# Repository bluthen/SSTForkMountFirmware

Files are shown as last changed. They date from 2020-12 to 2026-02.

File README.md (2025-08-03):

# SST Forkmount

This repo contains the electronic designs and software for [StarSync Trackers](https://starsynctrackers.com/)
computerized forkmount equatorial mounts. It was designed to work with SST hardware but should work with any fork mount
that uses steppers for motors.

## Component Structure

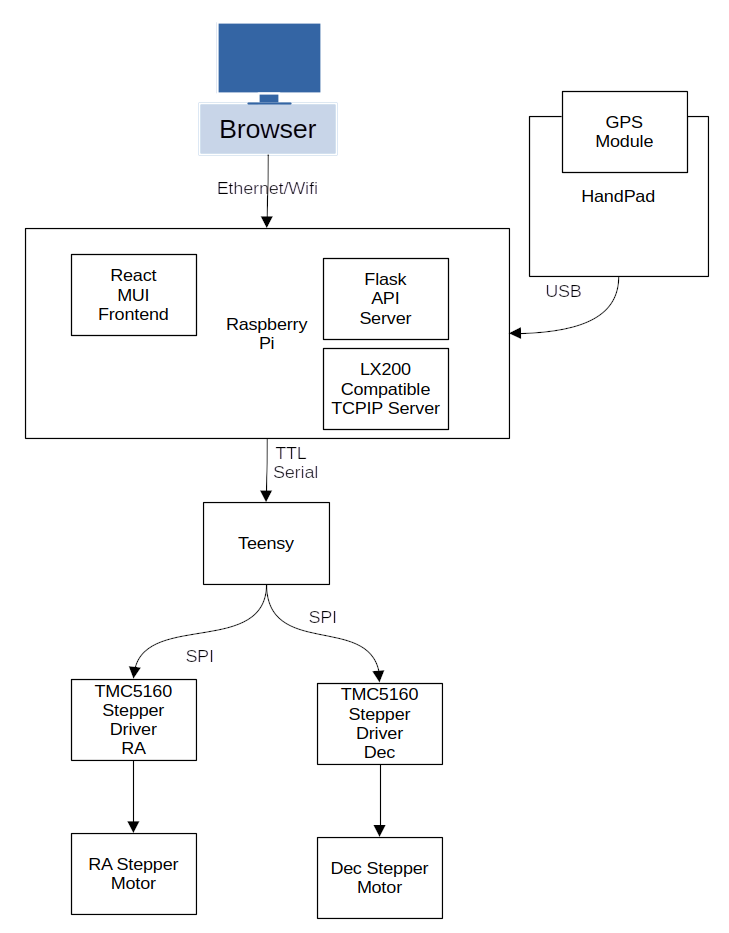
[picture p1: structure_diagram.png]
Diagram image on how the different components work together to make up the mount


Below it tries to describe

* Computer connects to the mount through Ethernet or Wifi and control the telescope in one of the following ways.
    * A web browser [SST Discovery Tool](https://github.com/bluthen/SSTForkMountDiscovery)
    * software capable of communicating through a LX200 protocol
* Handpad is a device attached through a USB cable
    * It has a GPS moduled embedded inside it that can give the telescope accurate time and location.
    * Has a interface to control the telescope without a computer attached, with goto and manual slew functions.
* Raspberry pi has a controller board (Pi Hat) attached to it and has three main components.
    * Flask API Server - Provides a REST like API to control the telescope
    * React MUI Frontend - web based user interface to communcate with the API Server
    * LX200 Compatible TCPIP Server - An alternative way to control the telescope through a dedicated TCP/IP Port.
* Motor Control Chain
    * Microcontroller (Teensy) - The Raspberry pi has a controller board attached and communicates with it through TTL
      Serial.
    * The Microcontroller (Teensy) - communicates with stepper drivers using SPI Protocol and step/direction protocol.
    * The stepper drivers (TMC5160) - controls the RA/Dec steppers to point the telescope

# Project directory structure

* [electronics](electronics) - Files related to the hardware of: Handpad, serial to ethernet, main controller
    * [enclosures](electronics/enclosures) - Enclosures to house electronics
    * [firmware](electronics/firmware) - Microcontroller firmware
    * [pcb](electronics/pcb) - Schematic and PCB files
* [piside](piside) - Software the run on the Pi.
    * [client_advanced_slew_limits](piside/client_advanced_slew_limits) - Slew limits UI component
    * [client_main](pisiude/client_main) - The Material UI web client
    * [server](piside/server) - Flask API Server

# TODOs

* Improve a test Error modeling
    * Add Star Alignment to handpad that uses the error modeling feature
    * Good prompts for error modeling/alignment to web ui
* Script and instructions to generate object and city elevation database `ssteq.sqlite`
* More python type-hinting
* Switch from Flask to [FastAPI](https://fastapi.tiangolo.com/)
* Cleanup files piside/server in director submodules
* Better testing of encoder usage
* Easier pi setup
* Instructions for settings.json for docker usage
* Alt/Az Mode

# Screenshots

Screen shots of the web client.

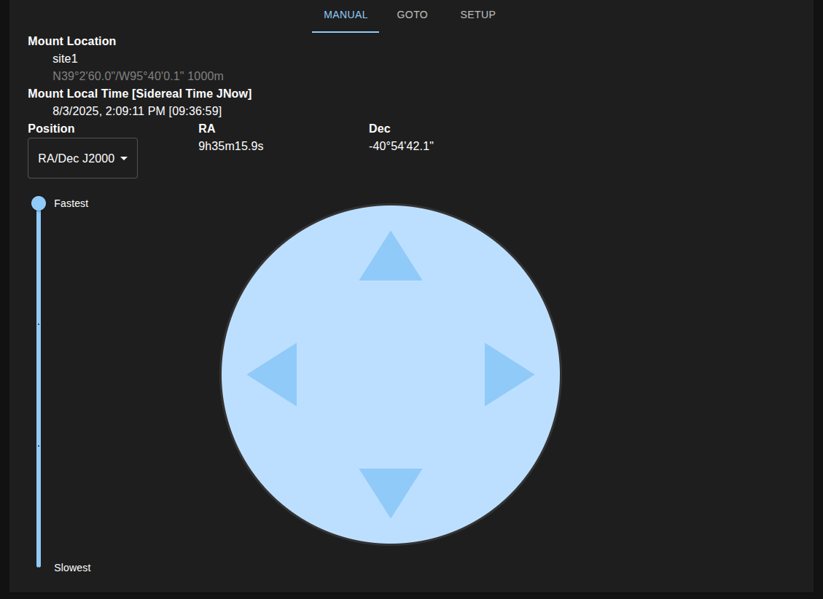
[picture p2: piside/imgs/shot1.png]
Screen shot of web client software running, circle in middle control directions, side vertical slider for speed.


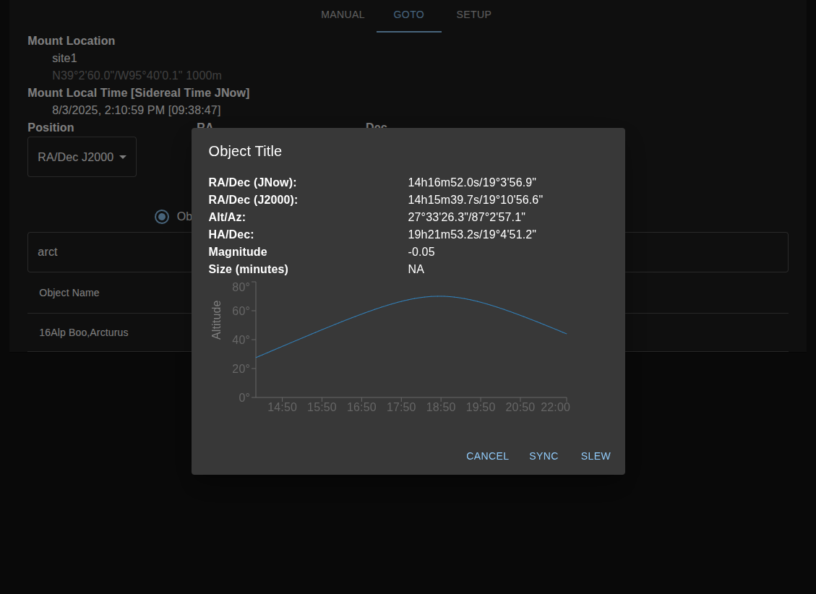
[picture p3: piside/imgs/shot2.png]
Screen shot of web client software running, a graph with time and altitude of Arcuturus with coordinates listed


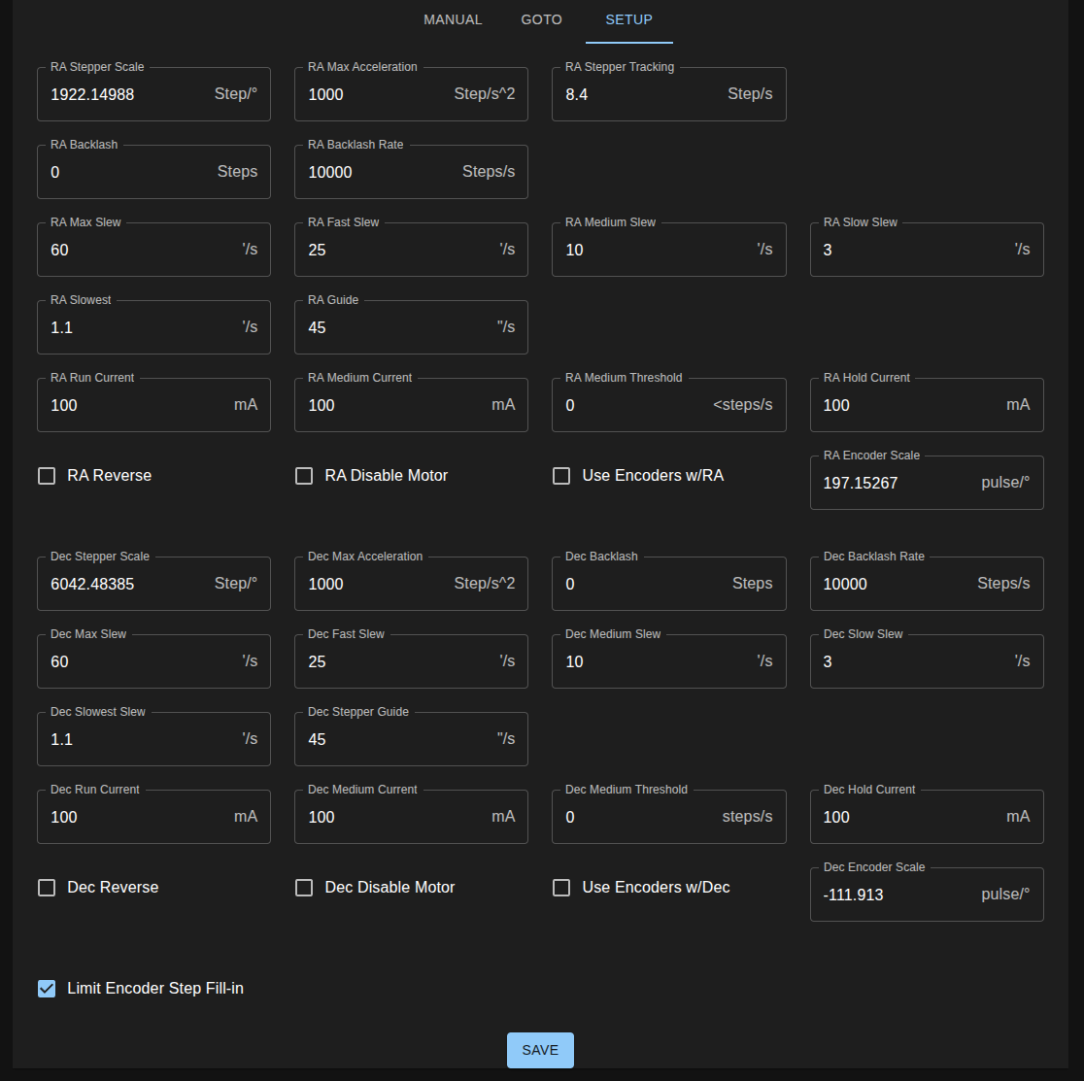
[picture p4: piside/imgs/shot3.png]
Screen shot of web client software running, advanced configuration window showing settings like steps per degrees, backlash, acceleration


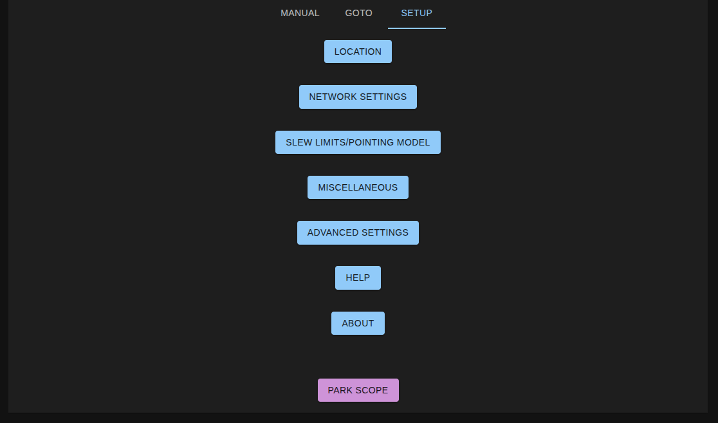
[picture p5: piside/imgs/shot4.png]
Screen shot of web client software running, setup menu with a set of buttons to different configuration screens


# Related projects

If you are interested in this project, some of these other open source projects might interest you.

* [OnStep](https://github.com/hjd1964/OnStep)
* [AstroEQ](https://www.astroeq.co.uk/)
* [TeenAstro](https://groups.io/g/TeenAstro)

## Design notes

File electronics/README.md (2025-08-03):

# SST Electronics Hardware

## PiHat/SSTFork Stepper Micro

This is the electronics that take communication from the Pi and control the stepper motors.

## Handpad

This is the electronics of the handpad. A handheld device, with a display, to control the telescope mount.

## Serial to Ethernet

This is a small device that creates a serial port on the host computer and sends back and forth all communication on the
serial port to a IP_ADDRESS:Port through Ethernet.

This could be handy for older software that can only communicate with LX200 Protocol through a serial port.

**Computer** <-USB Serial-> **serial_to_ethernet** <-Ethernet-> **Device/Fork Mount**

# Directroy Structure

See each section for more information.

* [enclosures](enclosures) - Enclosure to house electronics
* [firmware](firmware) - Microcontroller firmware files
* [pcb](pcb) - Schematic and PCB for electronics

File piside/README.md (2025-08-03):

# PiSide - Software that runs on the Pi

Screen shot of web client software running, circle in middle control directions, side vertical slider for speed.

Screen shot of web client software running, a graph with time and altitude of Arcuturus with coordinates listed

Screen shot of web client software running, advanced configuration window showing settings like steps per degrees, backlash, acceleration

Screen shot of web client software running, setup menu with a set of buttons to different configuration screens

# Docker compose

You can run the software in docker with a simulated microcontroller board.

* `settings.json` - needs to be set up correctly
* `ssteq.sqlite` - needs to be generated (gen script and documentation are on TODO list)
* `server/simulation_files` - may need to be set up

```bash
docker compose build
docker compose up
```

Open browser to: [http://localhost:5001](http://localhost:5001)

# Package Management: Local Development vs on Pi

Two package managers are used depending on if you are development on your desktop or development/running on the Pi.
Mainly so the package manager could be configured to utilize [Pi Wheels](https://www.piwheels.org/)

* [Pipenv](https://pipenv.pypa.io/en/latest/) was used for dependencies on the PI. Here we are able to
  utilize [Pi Wheels](https://www.piwheels.org/)
* [Poetry](https://python-poetry.org/) is used for desktop development

# Directory structure

* [server](server) - API Server
* [client_main](client_main) - Material UI based web client
* [client_advanced_slew_limits](client_advanced_slew_limits) - A web interface sub app to set slew limits written in
  jquery
* [setup](setup) - Setup documentation and files

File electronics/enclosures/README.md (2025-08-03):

# Enclosures

**NOTE: For handpad enclosures see [handpad](handpad)**

The enclosures are designed in [FreeCad](https://www.freecad.org/).

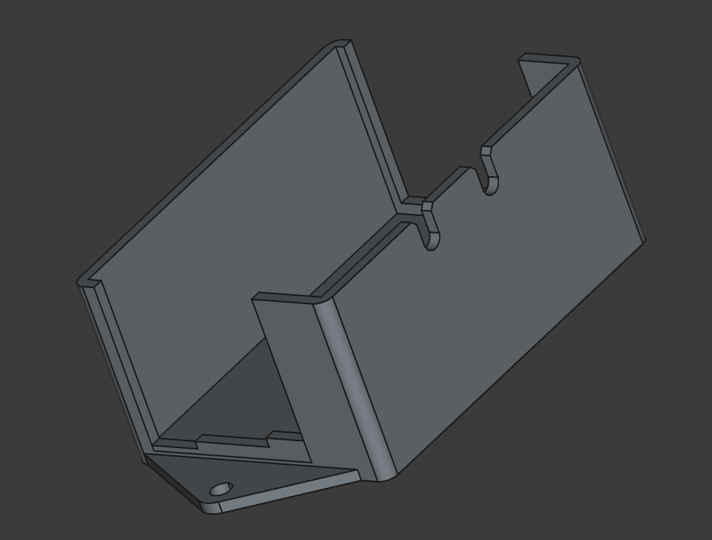
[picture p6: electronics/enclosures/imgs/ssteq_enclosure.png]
Render of main electronics enclosure model


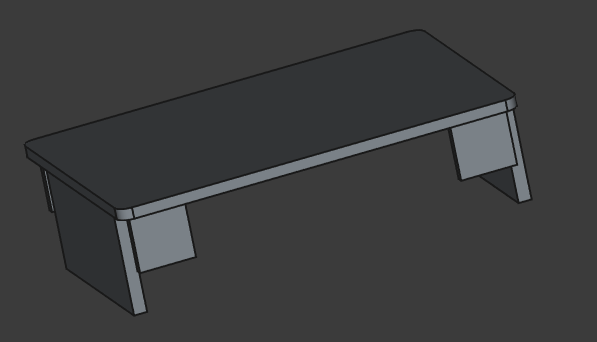
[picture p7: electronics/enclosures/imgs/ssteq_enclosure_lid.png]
Render of main electronics enclosure lid model


Render of a standoff model

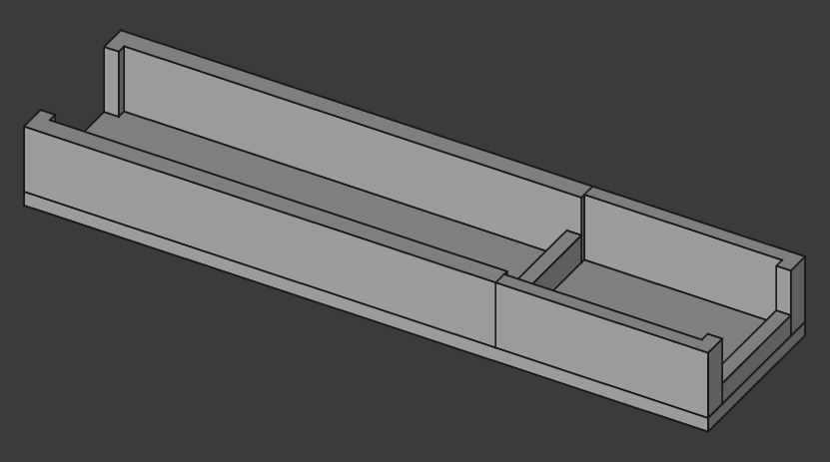
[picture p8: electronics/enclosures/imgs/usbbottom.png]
Render of Enclosure to hold Serial to Ethernet model bottom


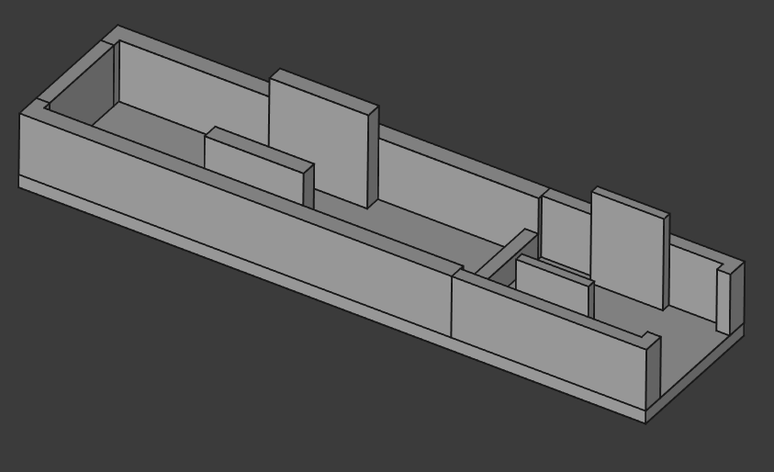
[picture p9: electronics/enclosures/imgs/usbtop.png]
Render of Enclosure to hold Serial to Ethernet model top


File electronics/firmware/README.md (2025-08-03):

# Electronics Firmware

This contains the firmware for microcontrollers.

* [sstfork_stepper_micro](sstfork_stepper_micro) - Firmware that controls the stepper drivers/steppers.
* [handpad](handpad) - Firmware for the microcontroller in the handpad.
* [serial_to_ethernet](serial_to_ethernet) - Firmware for the microcontroller the serial to ethernet bridge.

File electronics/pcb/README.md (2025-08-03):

# PCBs and Schematics

The PCBs are made in an Open Source Electronics Design Suite [KiCad](https://kicadstudio.com/).

## PiHat (Motor Controller)

The device that takes communication from the Pi that controls the stepper motors.

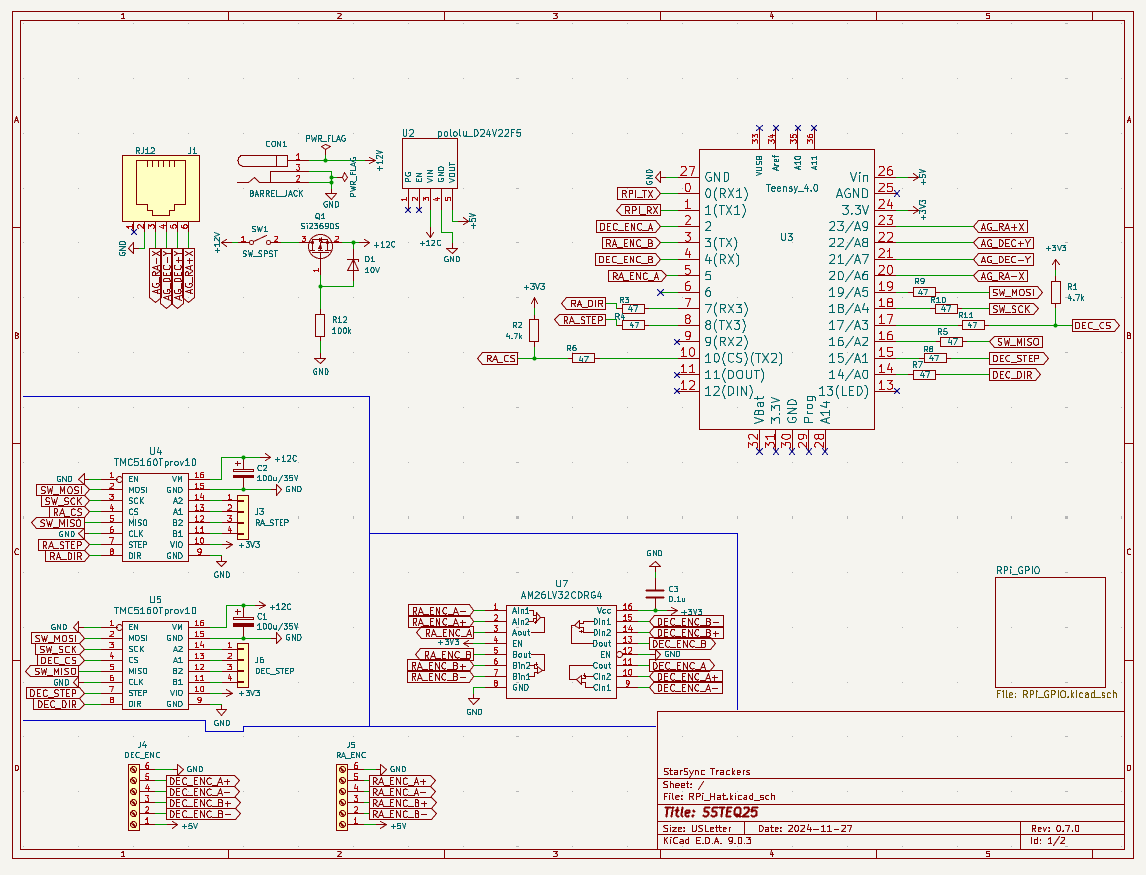
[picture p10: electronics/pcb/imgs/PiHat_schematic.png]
Screenshot from KiCad of PiHat schematic


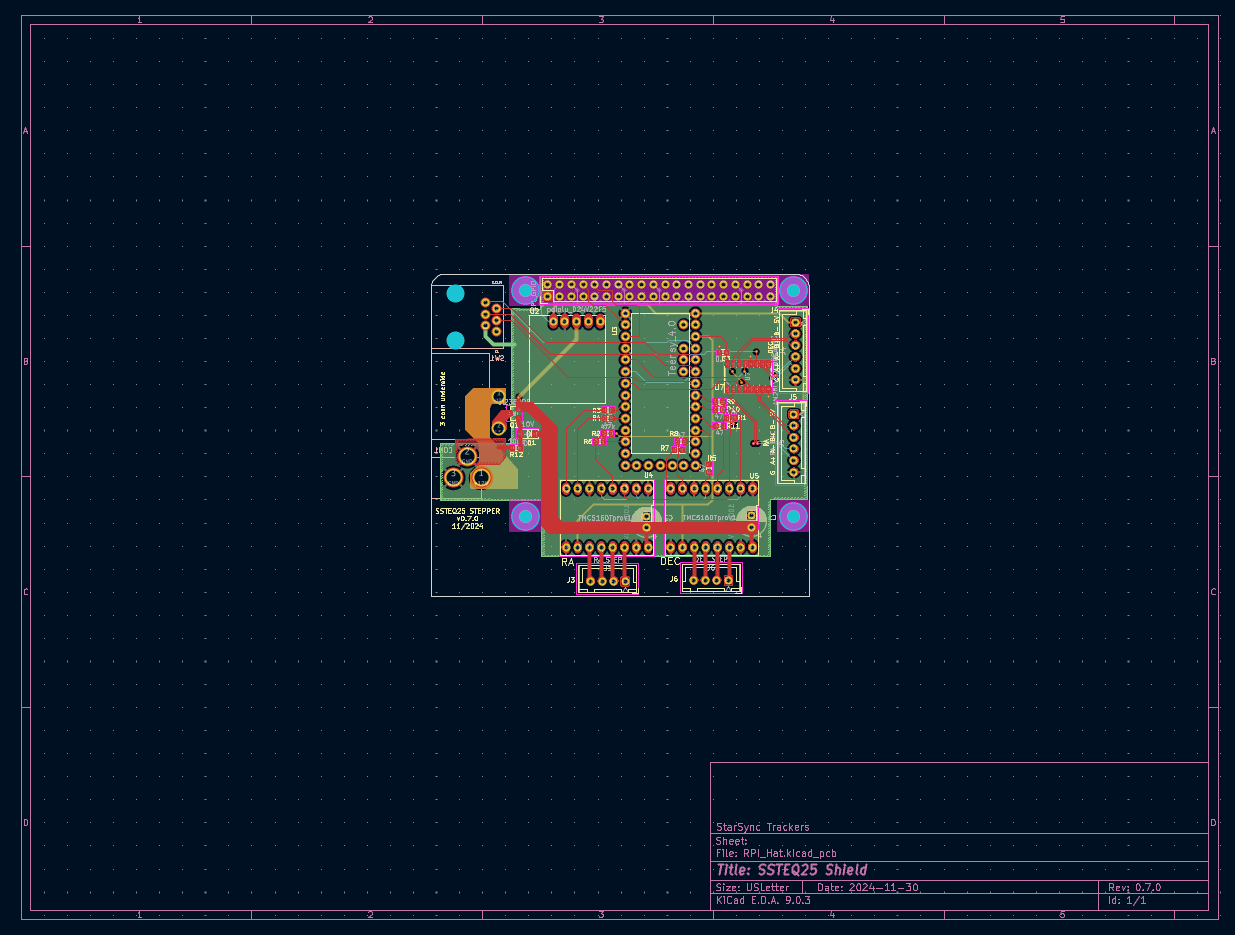
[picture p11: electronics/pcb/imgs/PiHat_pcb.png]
Screenshot from KiCad of PiHat PCB Layout


## Handpad

Handpad that lets you control the mount without a computer. Useful when next to the mount or using it for visual work.

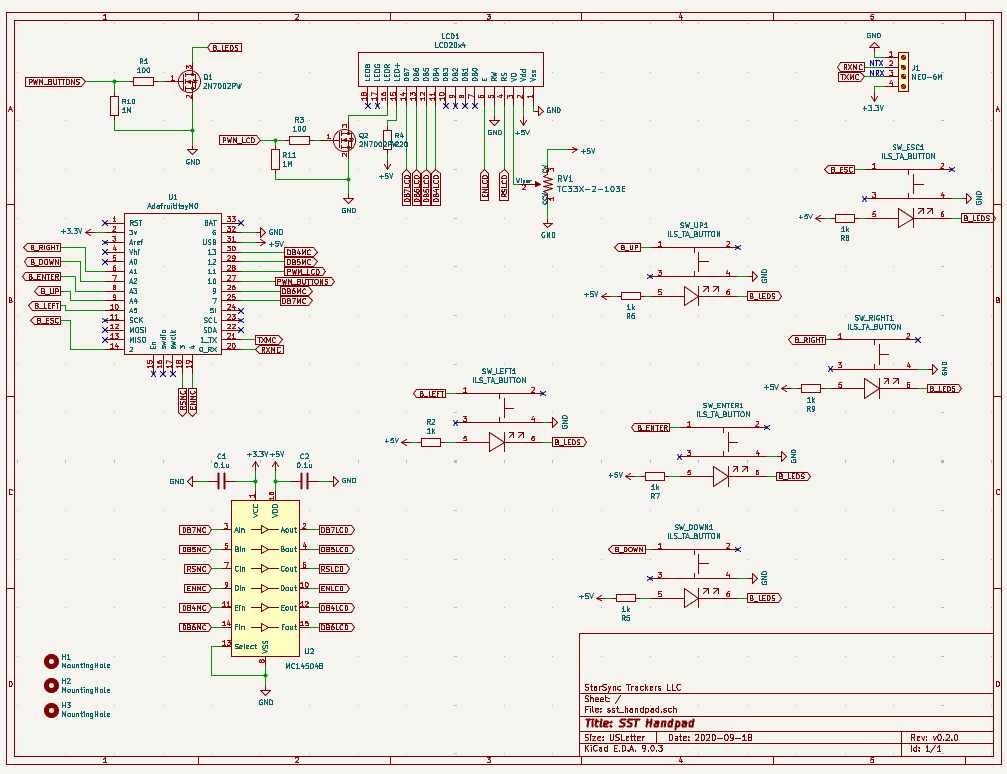
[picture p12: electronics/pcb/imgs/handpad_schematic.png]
Screenshot from KiCad of Handpad schematic


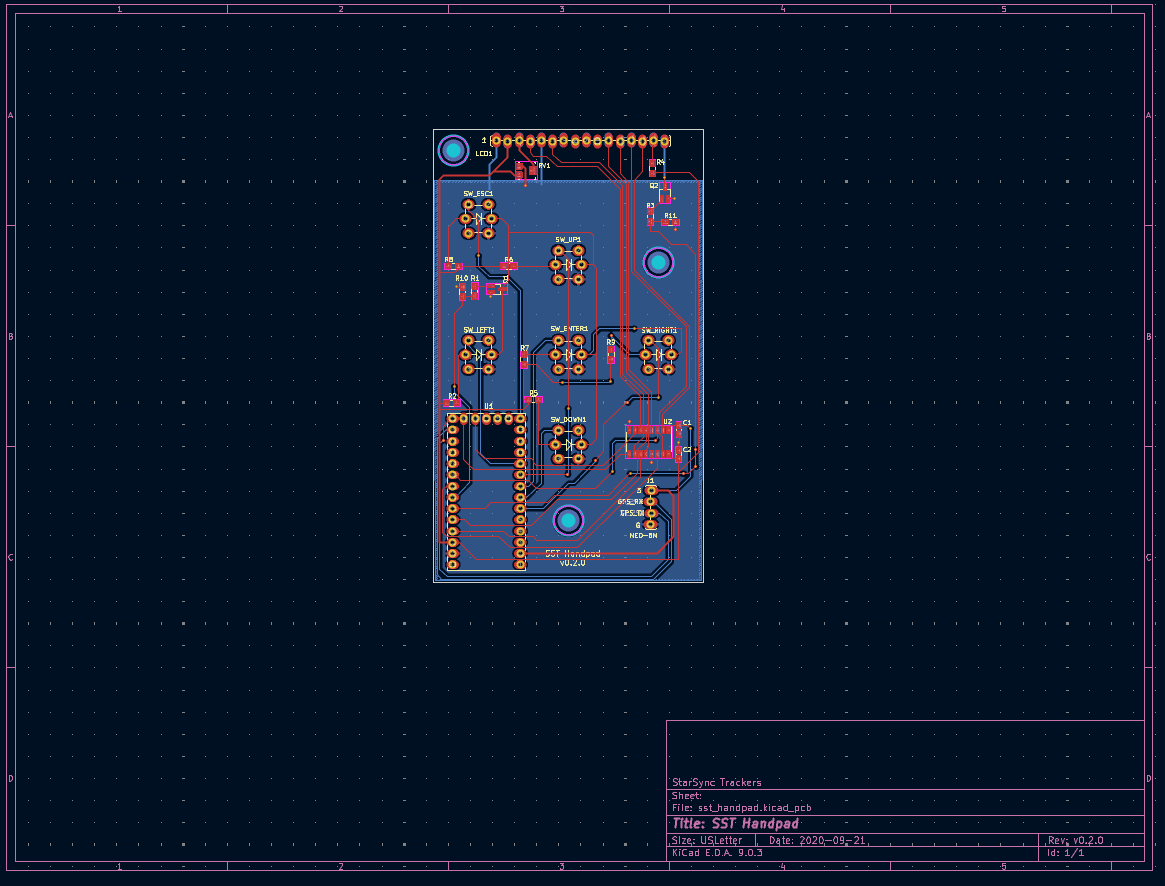
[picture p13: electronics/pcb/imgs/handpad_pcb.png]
Screenshot from KiCad of Handpad PCB Layout


# Directory Structure

* [BOM](BOM) - Bill Of Materials - spreadsheets of electronics components needed to build the device.
* [handpad](handpad) - KiCad handpad files.
* [PiHat](PiHat) - KiCad PiHat (Motor Controller) files.

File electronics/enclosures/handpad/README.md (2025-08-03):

# Handpad enclosure

Enclosure to hold handpad electronics.

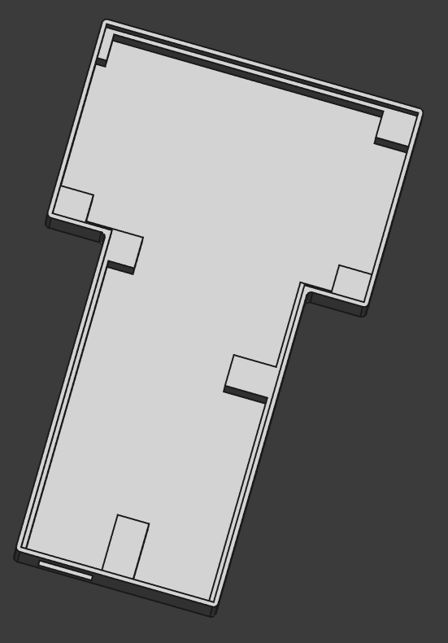
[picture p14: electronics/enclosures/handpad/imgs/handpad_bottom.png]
Render of bottom handpad model


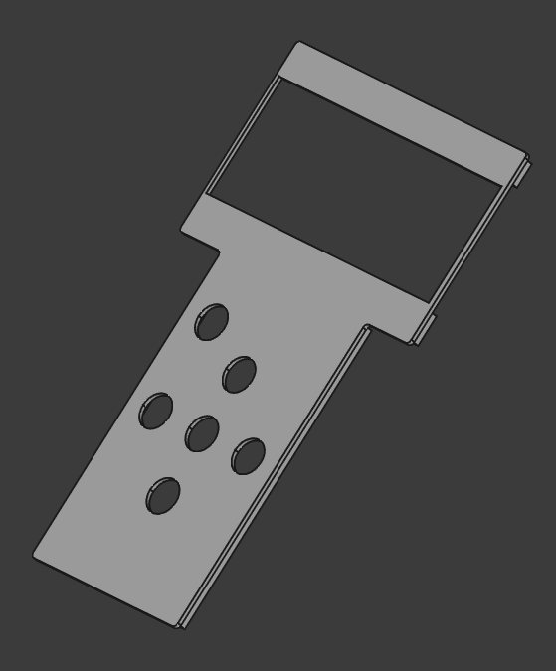
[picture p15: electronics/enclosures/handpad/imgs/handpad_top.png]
Render of top handpad model


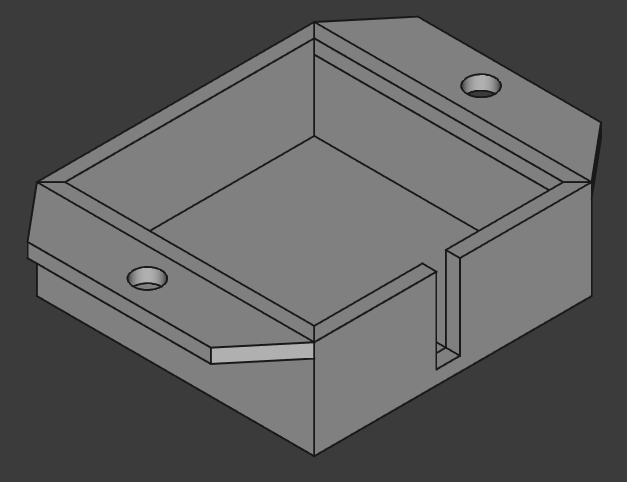
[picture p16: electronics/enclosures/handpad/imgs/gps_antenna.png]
Render of gps antenna box model


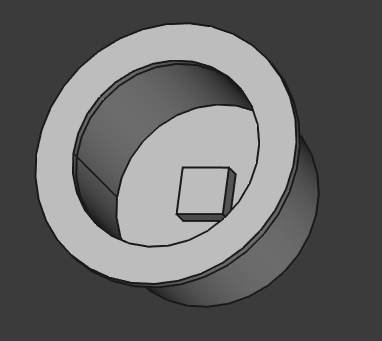
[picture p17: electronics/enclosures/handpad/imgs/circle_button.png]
Render of circle button model


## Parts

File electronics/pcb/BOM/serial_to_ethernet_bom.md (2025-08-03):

* Teensy 4.1 - https://www.pjrc.com/store/teensy41.html
* Ethernet Kit for Teensy 4.1 - https://www.pjrc.com/store/ethernet_kit.html

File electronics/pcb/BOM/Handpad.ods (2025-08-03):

Labels | Part | Quantity | Source | 2nd Source
SW_LEFT1, SW_DOWN1, SW_RIGHT1, SW_UP1, SW_ENTER1, SW_ESC1 |  |  | ILS TA250 10 (https://www.digikey.com/product-detail/en/ILS+TA250+10/108-ILSTA25010-ND/12352657/?itemSeq=337096876) | ILS TA180 10 (https://www.digikey.com/product-detail/en/ILS+TA180+10/108-ILSTA18010-ND/12352639/?itemSeq=337096880)
 | Tactile Pushbutton with Red LED | 6 | MPJA 34905 SW (https://www.mpja.com/SPST-NO-Tactile-Pushbutton-Switch-with-Red-LED-Pack-of-5/productinfo/34905+SW/) | Sparkfun: COM-10442 (https://www.sparkfun.com/products/10442)
Q1, Q2 | 2N700 N Mosfet, SOT-323 GSD | 2 | Digikey: 1727-4793-1-ND (https://www.digikey.com/product-detail/en/nexperia-usa-inc/2N7002PW115/1727-4793-1-ND/2531274)
U1 | ItsyBitsy M0 for CircuitPython | 1 | Adafruit: 3727 (https://www.adafruit.com/product/3727)
 | RGB Blacklight negative LCD 20x4 | 1 | Adafruit: 498 (https://www.adafruit.com/product/498)
R1, R3 | 100 ohm 0603 resistor | 2 | Digikey: CR0603-JW-101ELFCT-ND (https://www.digikey.com/product-detail/en/bourns-inc/CR0603-JW-101ELF/CR0603-JW-101ELFCT-ND/3740983)
R2, R5, R6, R7, R8, R9 | 1k ohm 0603 resistor | 6 | Digikey: A129688CT-ND (https://www.digikey.com/product-detail/en/te-connectivity-passive-product/CRGCQ0603F1K0/A129688CT-ND/8577520)
R10,R11 | 1M ohm 0603 resistor | 2 | Digikey: CR0603-JW-105ELFCT-ND (https://www.digikey.com/product-detail/en/bourns-inc/CR0603-JW-105ELF/CR0603-JW-105ELFCT-ND/3740985)
R4 | 220 ohm 0603 resistor | 1 | Digikey: 118-CR0603-JW-221ELFCT-ND (https://www.digikey.com/product-detail/en/bourns-inc/CR0603-JW-221ELF/118-CR0603-JW-221ELFCT-ND/3925350)
U2 | 4505 IC SOIC-16 | 1 | Digikey: MC14504BDR2GOSCT-ND (https://www.digikey.com/product-detail/en/on-semiconductor/MC14504BDR2G/MC14504BDR2GOSCT-ND/1139680)
C1, C2 | 0.1uF 0603 capacitor | 2 | Digikey: 1276-1000-1-ND (https://www.digikey.com/product-detail/en/samsung-electro-mechanics/CL10B104KB8NNNC/1276-1000-1-ND/3889086)
RV1 | 10k trimmer pot | 1 | Digikey: TC33X-103ECT-ND (https://www.digikey.com/product-detail/en/bourns-inc/TC33X-2-103E/TC33X-103ECT-ND/612911)
 | NEO GPS module
 | Micro USB cable
 | Right Angle Male Headers |  | Digikey: S1111EC-40-ND (https://www.digikey.com/product-detail/en/sullins-connector-solutions/PRPC040SBAN-M71RC/S1111EC-40-ND/2775294)
 | Female Crimp Pins |  |  | https://www.pololu.com/product/1930
 | Female Crimp Housing |  |  | https://www.pololu.com/category/70/crimp-connector-housings
 | 2x(1x6, 1x4)
 |  |  | https://www.digikey.com/en/products/detail/harwin-inc/M20-1060400/3728193
 |  |  | https://www.digikey.com/en/products/detail/harwin-inc/M20-1060800/3728198
 |  |  | https://www.digikey.com/en/products/detail/amphenol-icc-fci/65240-016LF/1485782
 |  |  | https://www.digikey.com/en/products/detail/harwin-inc/M20-1160042/3728122
 |  |  | https://www.digikey.com/en/products/detail/amphenol-icc-fci/76347-301LF/1642308

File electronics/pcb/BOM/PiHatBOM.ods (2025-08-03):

Labels | Part | Source | 2nd Source
C1, C2 | 100uF/35V | Digikey: 732-8737-1-ND (https://www.digikey.com/en/products/detail/w-rth-elektronik/860010573007/5728686)
C3 | 0603 0.1uF/10V capacitor | Digikey: 1276-1000-1-ND (https://www.digikey.com/product-detail/en/samsung-electro-mechanics/CL10B104KB8NNNC/1276-1000-1-ND/3889086)
CON1 | DC 5.1mm power jack | Digikey: CP-202A-ND (http://www.digikey.com/product-detail/en/cui-inc/PJ-202A/CP-202A-ND/252007)
J1 | 6P6C - RJ12 socket | Digikey: AE10383-ND (https://www.digikey.com/product-detail/en/assmann-wsw-components/A-2004-1-4-LP-N-R/AE10383-ND/2183634) | Sparkfun: 132 (https://www.sparkfun.com/products/132)
J2 | 2x20 tall female header .1 pitch ( 5mm x 51mm x 16.5mm / 0.2" x 2" x 0.65") 13.5mm insulator | Digikey: 1568-PRT-16764-ND (https://www.digikey.com/en/products/detail/sparkfun-electronics/PRT-16764/12686344) | Adafruit: 1992 (https://www.adafruit.com/product/1992)
SW1 | Rocker Switch SPST Right Angle | Digikey: EG5626-ND (https://www.digikey.com/product-detail/en/e-switch/RA1H1C112R/EG5626-ND/3778069)
U2 | 5V, 3.5A Step-Down Voltage Regulator Module | Sparkfun: COM-21256 (https://www.sparkfun.com/products/21256)
U2* | Heat Sink
U2** | 5V, 2.5A Step-Down Voltage Regulator Module | Pololu: D24V22F5 (https://www.pololu.com/product/2858)
U3 | Teensy 4.0 | PJRC: Teensy 4.0 (https://www.pjrc.com/store/teensy40.html)
U3*
U4, U5 | TMC5160 BigTree driver carrier | Bigtree TMC5160 (https://www.aliexpress.us/item/3256803165301348.html?gatewayAdapt=glo2usa4itemAdapt)
U4*, U5* | 01x08 0.1 pitch Female Headers | Digikey: 732-61300811821-ND (https://www.digikey.com/en/products/detail/w%C3%BCrth-elektronik/61300811821/17737805)
J3, J6 | 01x04 0.1 pitch JST Male
J4, J5 | 01x06 0.1 inch pitch JST male
U7 | 16-SOIC Quad differential RX 3.3v | Digikey: 296-46285-1-ND (https://www.digikey.com/product-detail/en/texas-instruments/AM26LV32CDRG4/296-46285-1-ND/7033460)
D1 | Zener 10V, SOD123 | Digikey: BZT52C10-TPMSCT-ND (https://www.digikey.com/en/products/detail/micro-commercial-co/BZT52C10-TP/806052)
Q1 | P-CH MOSFET, TO-236 | Digikey: SI2369DS-T1-GE3￼ (https://www.digikey.com/en/products/detail/vishay-siliconix/SI2369DS-T1-GE3/4327735)
 | 0.1" pitch male headers | Digikey: A26514-40-ND (https://www.digikey.com/product-detail/en/4-103327-0/A26514-40-ND/297924)
R1, R2 | 4.7k 0603 resistor | Digikey: 1292-WR06X472JTLCT-ND (https://www.digikey.com/en/products/detail/walsin-technology-corporation/WR06X472-JTL/13242044)
R3, R4, R5, R6, R7, R8, R9, R10, R11, R12, R13, R14 | 47 0603 resistor | Digikey: 1292-WR06X470JTLCT-ND (https://www.digikey.com/en/products/detail/walsin-technology-corporation/WR06X470-JTL/13241762)
R15 | 100k 0603 resistor | Digikey: CR0603-JW-104ELFCT-ND (https://www.digikey.com/en/products/detail/bourns-inc/CR0603-JW-104ELF/2345098)
 | Raspberry Pi 3
 | 16 Gig Class 10+ micro sd card | Amazon: 16GB MicroSD card (https://www.amazon.com/Sandisk-Ultra-Micro-UHS-I-Adapter/dp/B073K14CVB?s=pc)
 | Electronics enclosure | 3d printed, using PLA or PETG
 |  | Digikey: S7012-ND (https://www.digikey.com/en/products/detail/sullins-connector-solutions/PPTC141LFBN-RC/810152)
 | Misc wires,heat shrink, solder
TOTAL:
https://www.digikey.com/en/products/detail/advanced-thermal-solutions-inc/ATS-EXL58-300-R0/5848390
Dual Brushed motor driver |  | Pololu: Dual MC33926 (https://www.pololu.com/product/1213)
Depricated
C1 | 100uF/35V capacitor, 8.3mmx8.3mm land size | Digikey: 732-8511-1-ND (https://www.digikey.com/en/products/detail/w%C3%BCrth-elektronik/865080545012/5728106)
U2 | 5V, 2.5A Step-Down Voltage Regulator Module | Pololu: D24V22F5 (https://www.pololu.com/product/2858)
U3 | Teensy LC | PJRC: TeensyLC (https://www.pjrc.com/teensy/teensyLC.html)
U4, U5 (option 1) | Pololu A4988 motor driver carrier | Pololu 1182 (https://www.pololu.com/product/1182)
U4, U5 (option 2) | Pololu TB67S249FTG | Pololu: TB67S249FTG (https://www.pololu.com/product/3096)

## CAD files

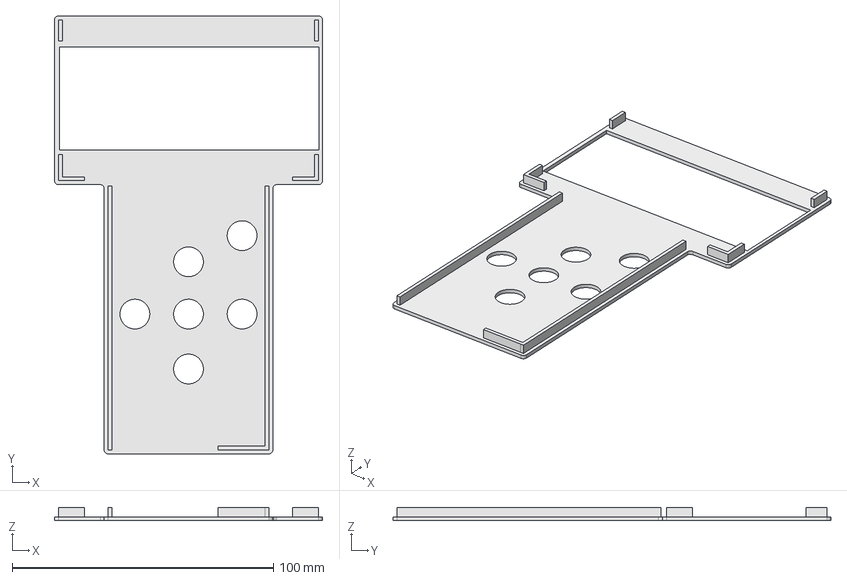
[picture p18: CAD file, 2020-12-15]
electronics/enclosures/handpad/top.FCStd
102.5 x 167.5 x 5.15 mm

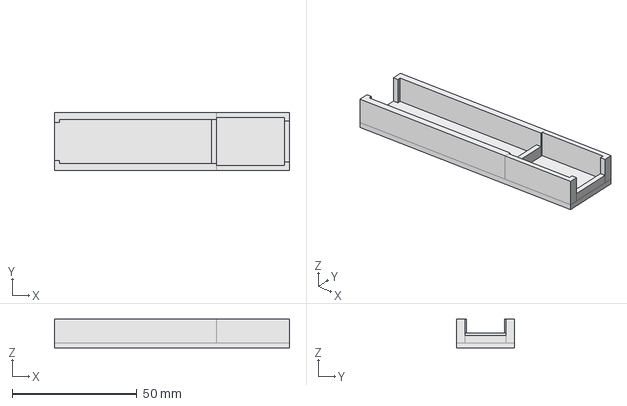
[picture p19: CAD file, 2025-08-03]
electronics/enclosures/USBSerialBottom.FCStd
94.2 x 23.1 x 11.5 mm

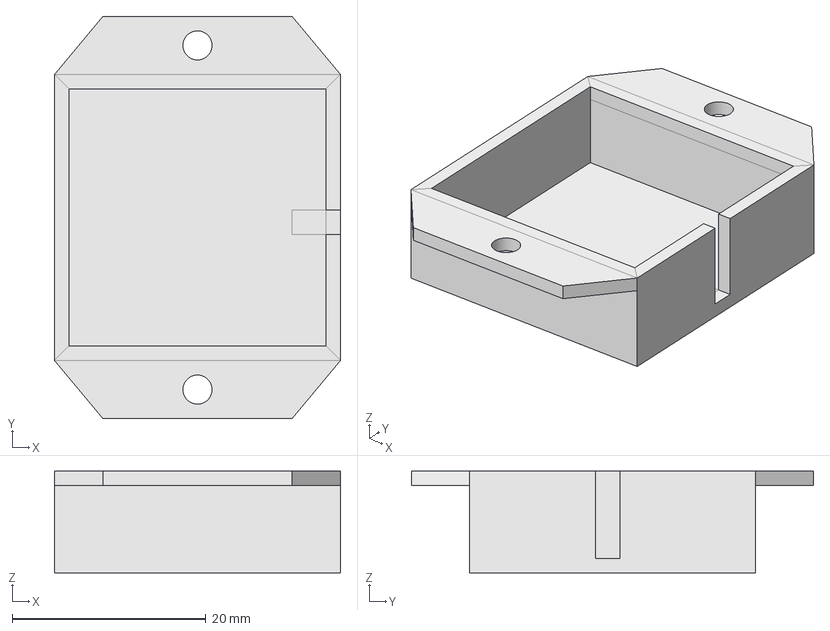
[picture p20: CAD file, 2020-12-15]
electronics/enclosures/handpad/gps_antenna.FCStd
29.5 x 41.5 x 10.5 mm

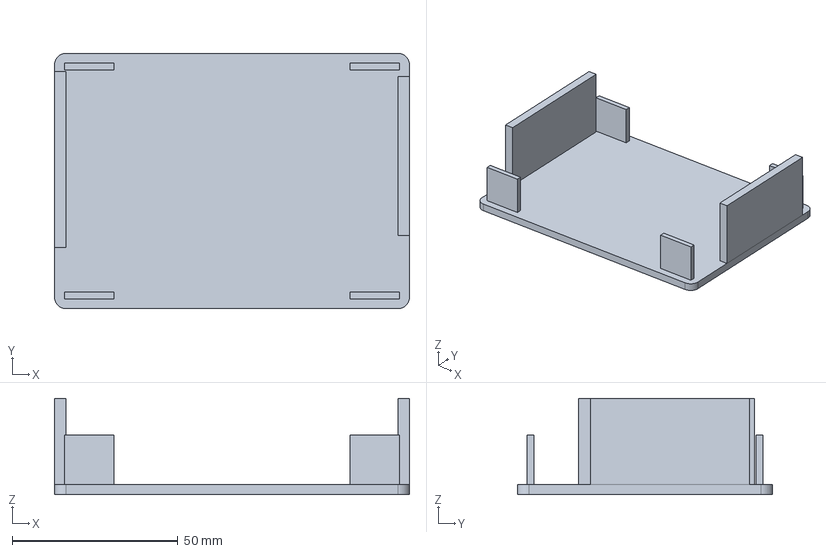
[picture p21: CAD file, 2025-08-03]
electronics/enclosures/ssteq_enclosurev0.7.0_lid.fcstd.FCStd
107.0 x 77.0 x 29.0 mm

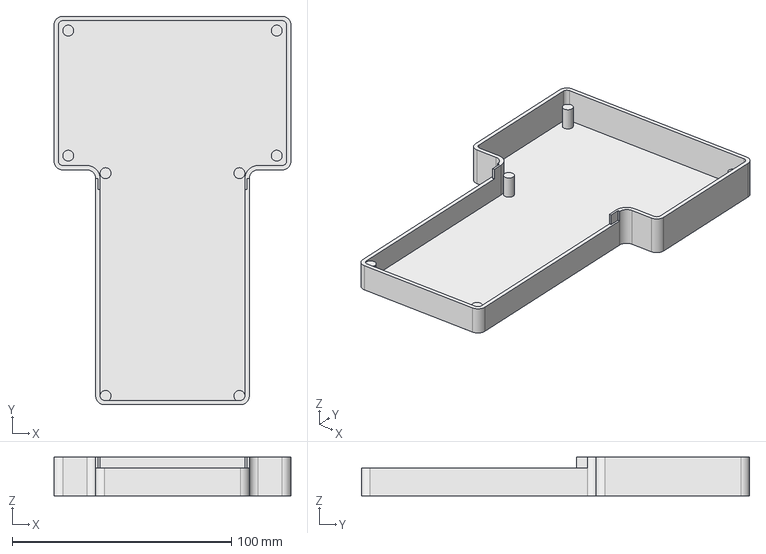
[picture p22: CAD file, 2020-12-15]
electronics/enclosures/handpad/bottom_north.FCStd
108.0 x 177.0 x 17.6 mm

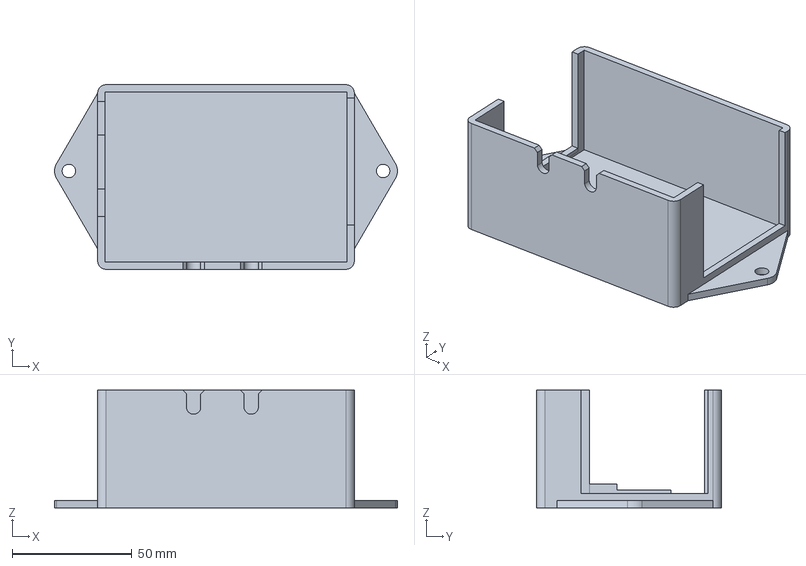
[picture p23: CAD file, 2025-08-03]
electronics/enclosures/ssteq_enclosurev0.7.0.fcstd
143.0 x 77.0 x 49.0 mm

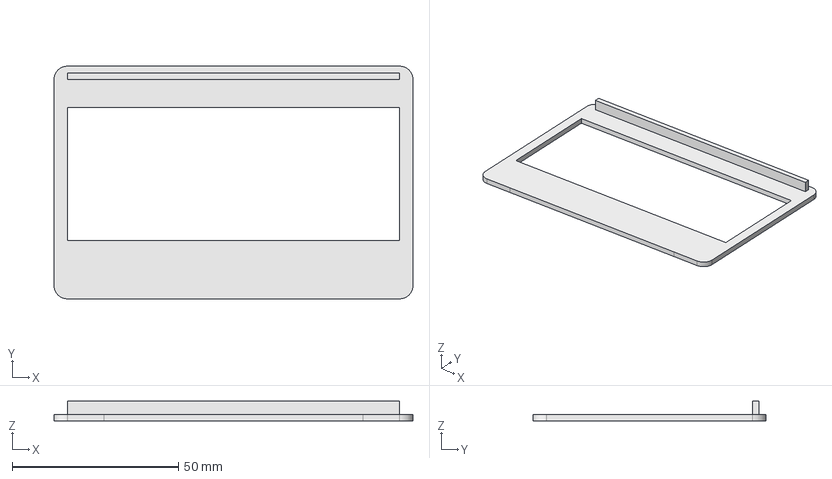
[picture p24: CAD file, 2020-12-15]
electronics/enclosures/handpad/top_north.FCStd
108.0 x 70.0 x 6.00 mm

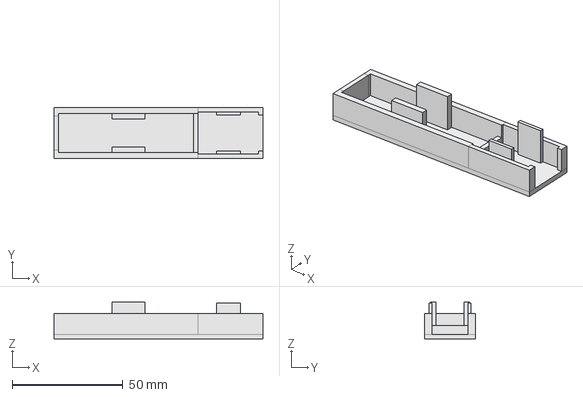
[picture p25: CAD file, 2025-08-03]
electronics/enclosures/USBSerialTop.FCStd
94.2 x 23.1 x 16.5 mm

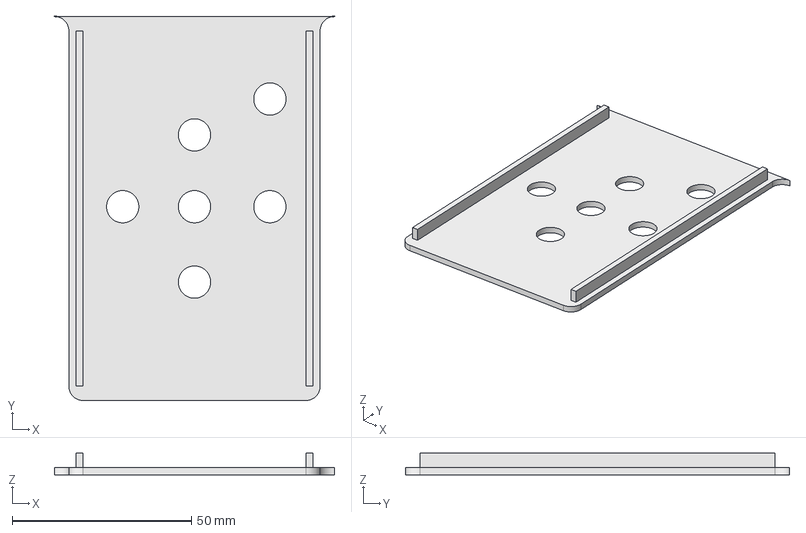
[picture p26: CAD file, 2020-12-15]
electronics/enclosures/handpad/top_south.FCStd
78.0 x 107.0 x 6.00 mm

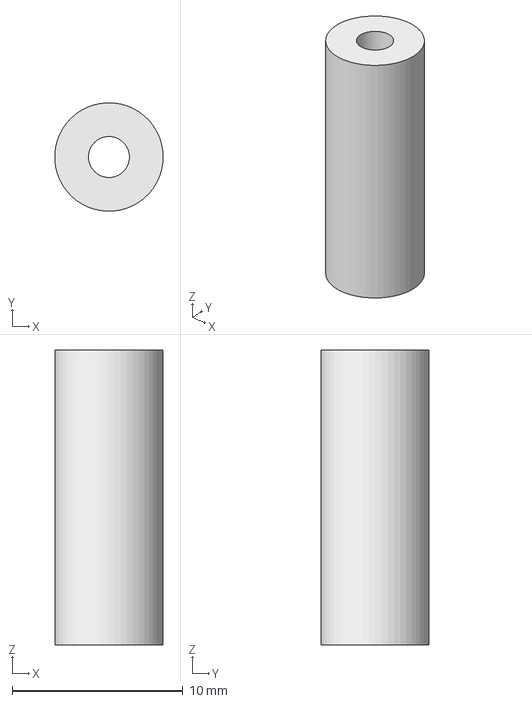
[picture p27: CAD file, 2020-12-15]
electronics/enclosures/standoff.FCStd
6.34 x 6.35 x 17.3 mm

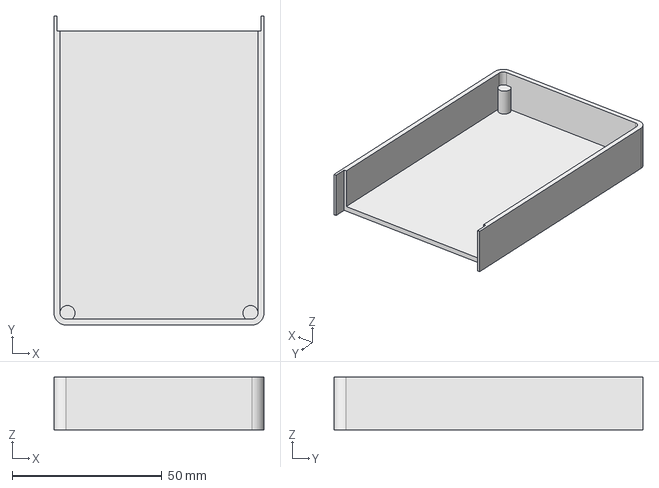
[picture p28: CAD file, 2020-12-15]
electronics/enclosures/handpad/bottom_south.FCStd
70.0 x 103.0 x 17.6 mm

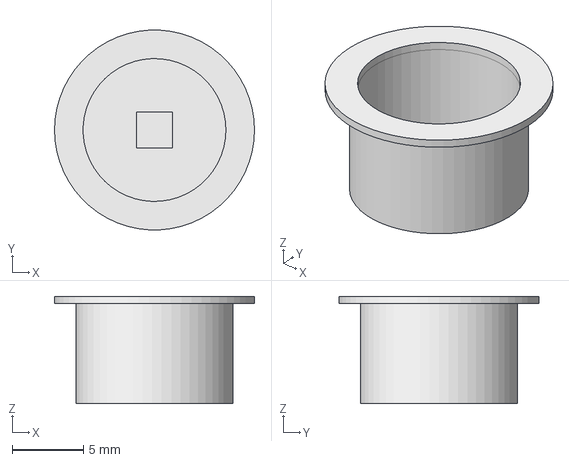
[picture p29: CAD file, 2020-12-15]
electronics/enclosures/handpad/circle_button.FCStd
14.0 x 14.0 x 7.50 mm

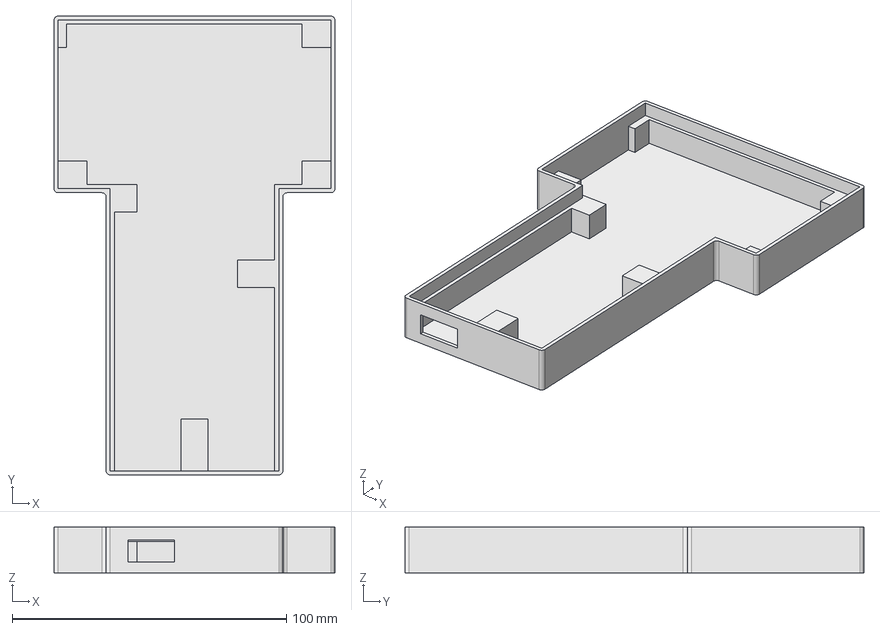
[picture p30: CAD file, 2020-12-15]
electronics/enclosures/handpad/bottom.FCStd
102.5 x 167.5 x 16.8 mm

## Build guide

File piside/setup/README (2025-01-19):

Raspberry pi imager to install image:
  Custom settings
  Set hostname: sstfork20240726
  Set username: pi / sstfork pwd
  Set locale
  Services: enable sshe: allow public key

#unzip 2021-01-11-raspios-buster-armhf-lite.zip 
#sudo dd if=2021-01-11-raspios-buster-armhf-lite.img of=/dev/sde bs=4M
#sync
e2fsck -f /dev/sde2
fdisk /dev/sde
  p
  d
  2
  n
  p
  2
  <original start>
  +13G
  N
  p
  n
  p
  3
  <partition 2's end>+1
  <enter>
  w
resize2fs /dev/sde2
mkfs.ext4 /dev/sde3
sync

# May need to power down and up the pi twice
# Logged onto Pi

sudo apt update --fix-missing && sudo apt upgrade -y
sudo reboot

sudo raspi-config
        system options ->    boot options -> desktop/cli -> console
        system options -> network -> no wait on boot
	interfacing options -> serial -> no -> yes
        advanced->network -> interfaces names -> no 

sudo reboot

sudo apt install -y python3-pip git libblas3 liblapack3 libatlas3-base ntp ntpdate ntpstat hostapd dnsmasq vim avahi-utils astrometry.net imagemagick libssl-dev libbz2-dev libncurses-dev libreadline-dev libffi-dev libsqlite3-dev lzma-dev

# append fstab
/dev/mmcblk0p3 /ssteq ext4 defaults,ro,noatime 0 2
systemctl daemon-reload
mkdir /ssteq
mount /ssteq
mount -o remount,rw /ssteq
mkdir -p /ssteq/piside/client_main
mkdir -p /ssteq/setup
chown -R pi /ssteq

pip3 install pipenv --break-system-packages

# Copy piside code: server, client_main, and client_advanced_slew_limits
#   cd copy piside
#   scp -r server pi@$IP:/ssteq/piside
#   scp -r client_advanced_slew_limits pi@$IP:/ssteq/piside
#   cd client_main
#   scp -r dist pi@$IP:/ssteq/piside/client_main/
#   cd ..
#   scp -r setup pi@$IP:/ssteq/
ln -s /ssteq/piside/client_main/dist /ssteq/piside/client_main/dist/static
# Copy object database

# in server folder as pi user
cd /ssteq/piside/server
export WORKON_HOME=/ssteq/piside/python_venvs
pipenv sync 

# udev teensy files for controller
sudo cp 49-teensy.rules /etc/udev/rules.d

sudo cp hostapd.conf /etc/hostapd/hostapd.conf
sudo bash -c "cat dnsmasq.conf.append >> /etc/dnsmasq.conf"
sudo bash -c "echo ssteq20250118 > /etc/hostname"
sudo cp interfaces.default /etc/network/interfaces.d/defaults

sudo cp autohotspot /usr/bin/autohotspot
sudo chown root:root /usr/bin/autohotspot
sudo chmod 755 /usr/bin/autohotspot
sudo cp networkstartup.sh /root/
sudo cp ctrl_dnsmasq.py /root/ctrl_dnsmasq.py
sudo chmod 755 /root/networkstartup.sh
sudo chmod 755 /root/ctrl_dnsmasq.py
sudo cp wpa_supplicant.conf /etc/wpa_supplicant/

systemctl disable apt-daily.service
systemctl disable apt-daily-upgrade.service
systemctl disable dnsmasq.service
systemctl disable hostapd.service
systemctl disable bluetooth.service
systemctl enable ntp.service

/etc/rc.local:
  /bin/hostname `cat /etc/hostname`

cp ssteq25.service /etc/systemd/system/
cp clearhomepyc.service /etc/systemd/system/
systemctl enable clearhomepyc.service 
systemctl enable ssteq25

# Disable storage logs /etc/systemd/journald.conf
```
Storage=volatile
RuntimeMaxUse=3M
```
# Set /etc/ssh/sshd_config to not allow password auth
```
PasswordAuthentication no
```

sudo bash /ssteq/setup/etc_symlinks_make.sh

# Edit cron
crontab -e
*/2 * * * * /usr/bin/autohotspot

raspi-config
   performance->Overlay FS -> Yes -> Yes write protect

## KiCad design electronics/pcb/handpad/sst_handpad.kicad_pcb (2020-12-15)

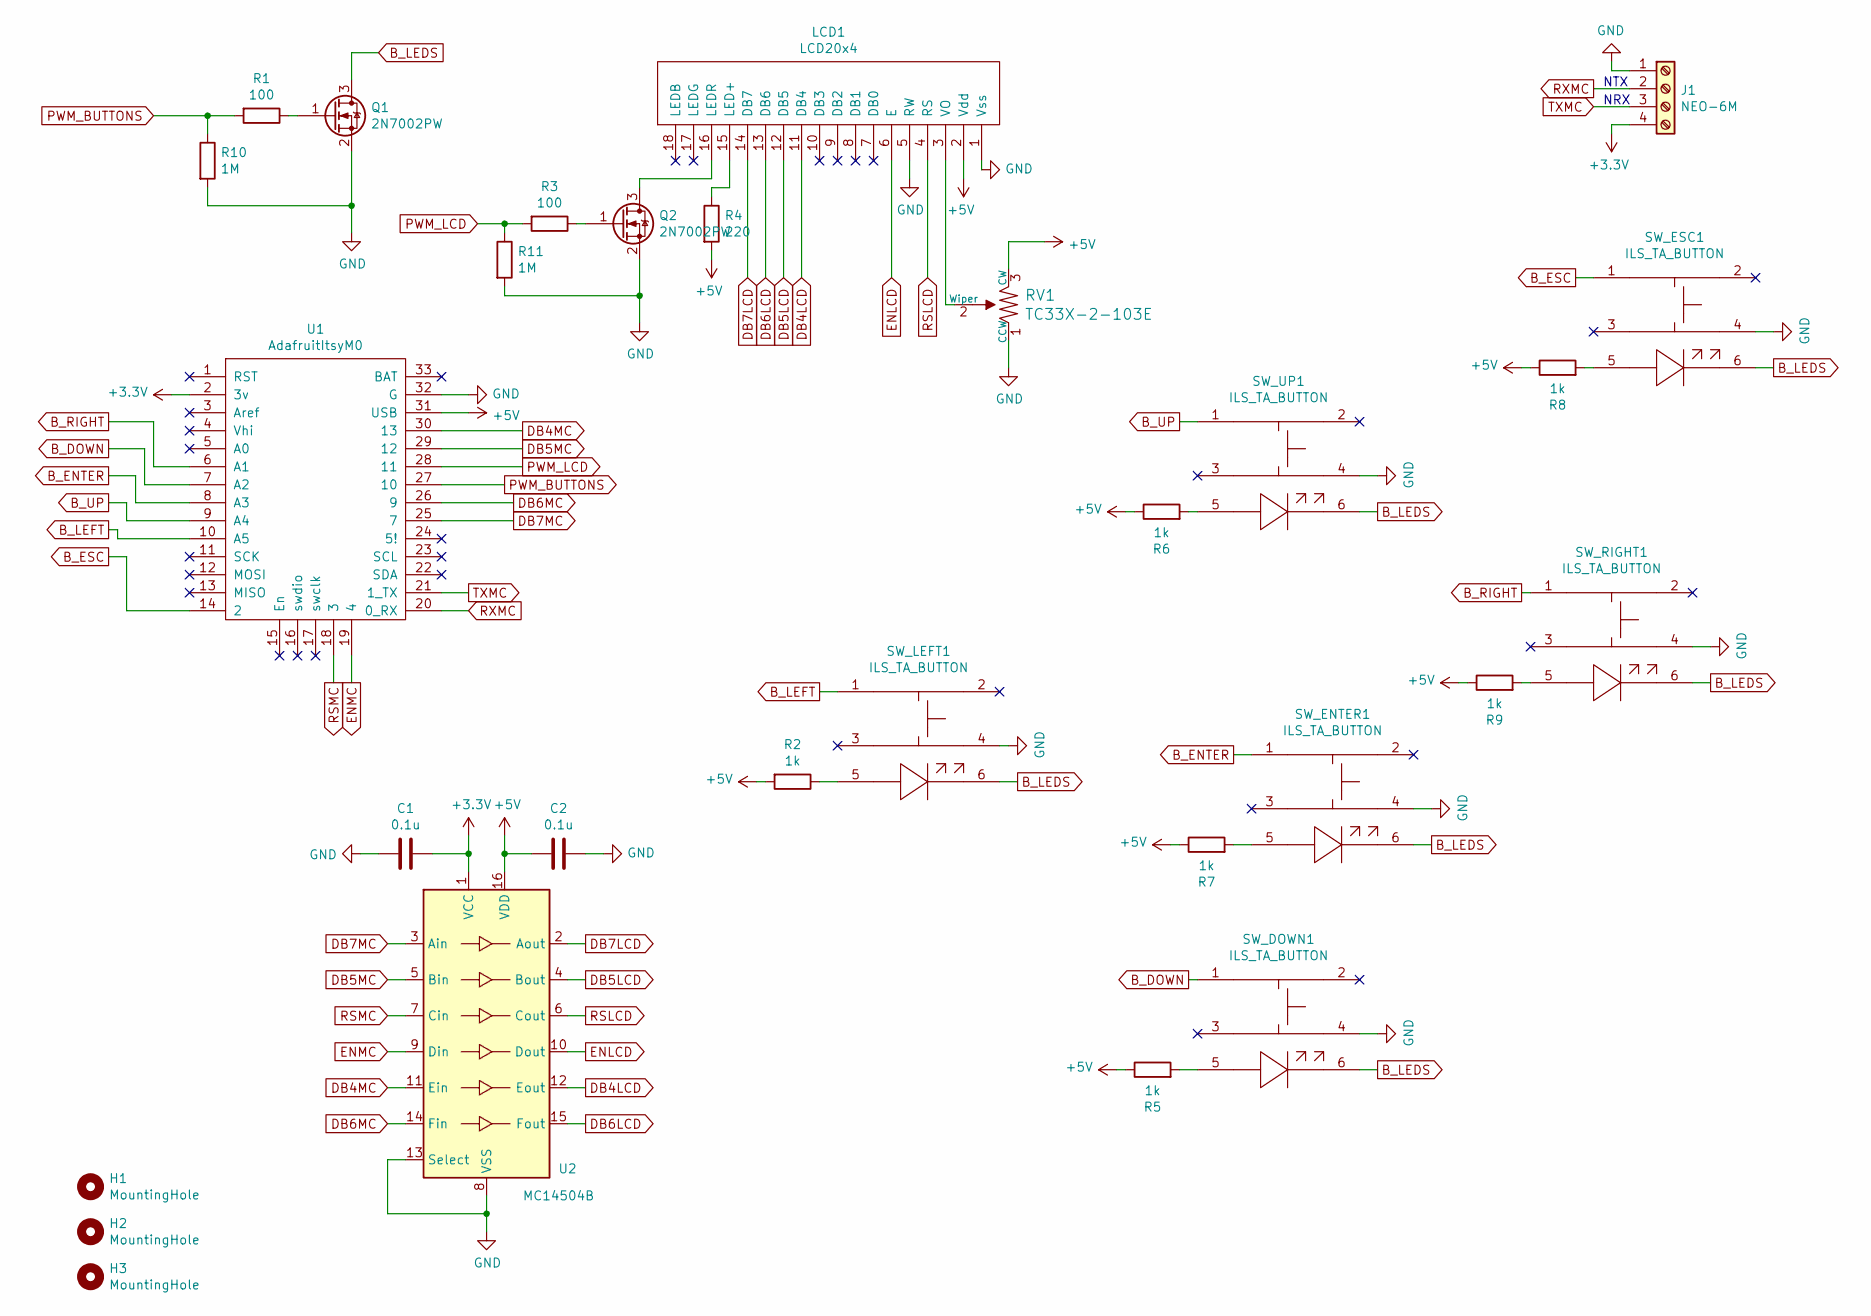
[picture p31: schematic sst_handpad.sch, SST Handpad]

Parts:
C1, C2: 0.1u; C_0603_HandSoldering
H1, H2, H3: MountingHole; MountingHole_3.2mm_M3
J1: NEO-6M; 1X04_LOCK_LONGPADS
LCD1: LCD20x4; 1X16_LOCK_LONGPADS
Q1, Q2: 2N7002PW; SOT-323_SC-70_Handsoldering
R1, R3: 100; R_0603_HandSoldering
R2, R5, R6, R7, R8, R9: 1k; R_0603_HandSoldering
R4: 220; R_0603_HandSoldering
R10, R11: 1M; R_0603_HandSoldering
RV1: TC33X-2-103E; Trimpot_3.8mmx3.6mm_TC33X-2-103E; MPN TC33X-2-103E; Digi-Key_PN TC33X-103ETR-ND
SW_DOWN1: ILS_TA_BUTTON
SW_ENTER1: ILS_TA_BUTTON
SW_ESC1: ILS_TA_BUTTON
SW_LEFT1: ILS_TA_BUTTON
SW_RIGHT1: ILS_TA_BUTTON
SW_UP1: ILS_TA_BUTTON
U1: AdafruitItsyM0; ItsyBitsyM0Exp
U2: MC14504B; SOIC-16_3.9x9.9mm_Pitch1.27mm

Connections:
+3V3: C1.2, J1.4, U1.2 (3v), U2.1 (VCC)
+5V: C2.2, LCD1.2 (Vdd), R2.2, R4.2, R5.1, R6.1, R7.1, R8.1, R9.1, RV1.3 (CW), U1.31 (USB), U2.16 (VDD)
B_DOWN: SW_DOWN1.1, U1.7 (A2)
B_ENTER: SW_ENTER1.1, U1.8 (A3)
B_ESC: SW_ESC1.1, U1.14 (2)
B_LEDS: Q1.3 (D), SW_DOWN1.6, SW_ENTER1.6, SW_ESC1.6, SW_LEFT1.6, SW_RIGHT1.6, SW_UP1.6
B_LEFT: SW_LEFT1.1, U1.10 (A5)
B_RIGHT: SW_RIGHT1.1, U1.6 (A1)
B_UP: SW_UP1.1, U1.9 (A4)
DB4LCD: LCD1.11 (DB4), U2.12 (Eout)
DB4MC: U1.30 (13), U2.11 (Ein)
DB5LCD: LCD1.12 (DB5), U2.4 (Bout)
DB5MC: U1.29 (12), U2.5 (Bin)
DB6LCD: LCD1.13 (DB6), U2.15 (Fout)
DB6MC: U1.26 (9), U2.14 (Fin)
DB7LCD: LCD1.14 (DB7), U2.2 (Aout)
DB7MC: U1.25 (7), U2.3 (Ain)
ENLCD: LCD1.6 (E), U2.10 (Dout)
ENMC: U1.19 (4), U2.9 (Din)
GND: C1.1, C2.1, J1.1, LCD1.1 (Vss), LCD1.5 (RW), Q1.2 (S), Q2.2 (S), R10.2, R11.2, RV1.1 (CCW), SW_DOWN1.4, SW_ENTER1.4, SW_ESC1.4, SW_LEFT1.4, SW_RIGHT1.4, SW_UP1.4, U1.32 (G), U2.8 (VSS), U2.13 (Select)
unnamed: LCD1.3 (VO), RV1.2 (Wiper)
unnamed: LCD1.15 (LED+), R4.1
unnamed: LCD1.16 (LEDR), Q2.3 (D)
unnamed: Q1.1 (G), R1.1
unnamed: Q2.1 (G), R3.1
unnamed: R2.1, SW_LEFT1.5
unnamed: R5.2, SW_DOWN1.5
unnamed: R6.2, SW_UP1.5
unnamed: R7.2, SW_ENTER1.5
unnamed: R8.2, SW_ESC1.5
unnamed: R9.2, SW_RIGHT1.5
PWM_BUTTONS: R1.2, R10.1, U1.27 (10)
PWM_LCD: R3.2, R11.1, U1.28 (11)
RSLCD: LCD1.4 (RS), U2.6 (Cout)
RSMC: U1.18 (3), U2.7 (Cin)
RXMC: J1.2, U1.20 (0_RX)
TXMC: J1.3, U1.21 (1_TX)

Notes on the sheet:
NTX
NRX

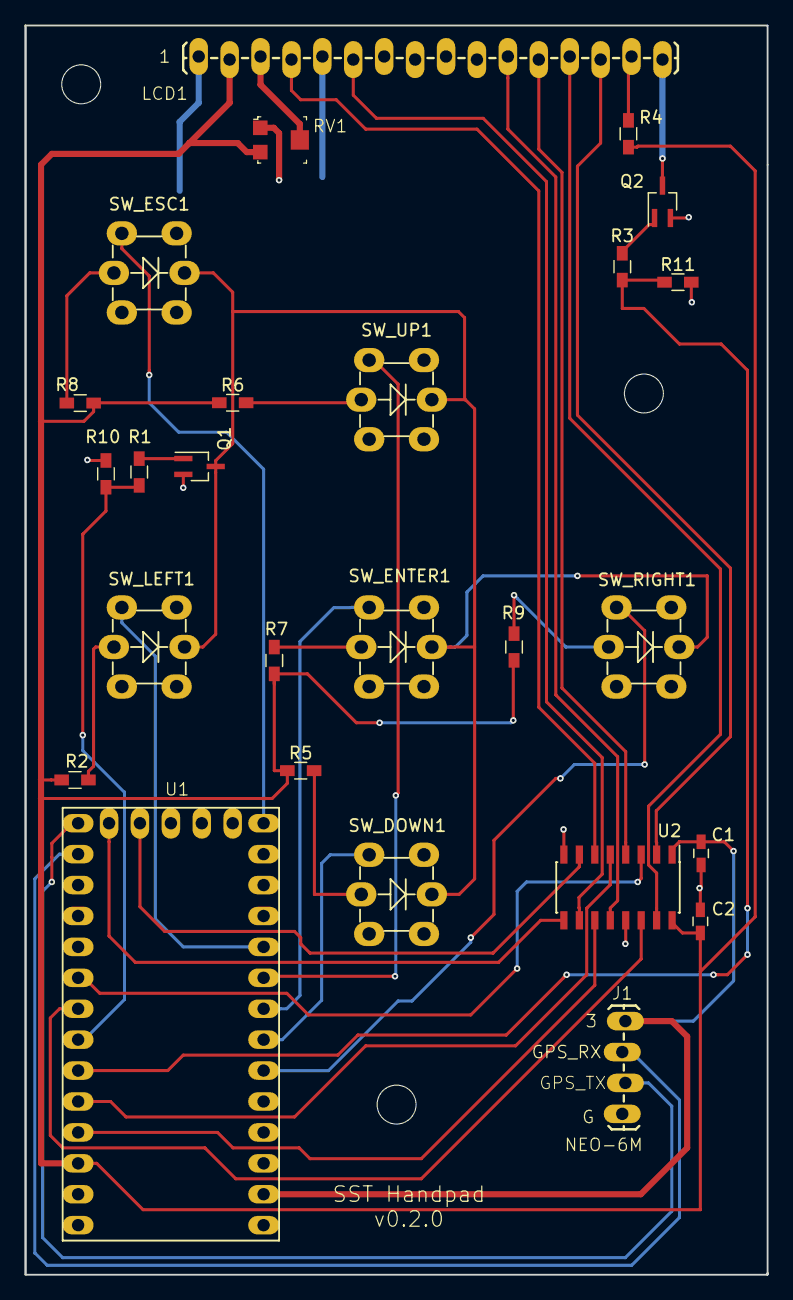
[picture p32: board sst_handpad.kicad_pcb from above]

Board: 2 copper layers, 61.0 x 102.6 mm, 29 parts (0 on the bottom side), 37 nets.

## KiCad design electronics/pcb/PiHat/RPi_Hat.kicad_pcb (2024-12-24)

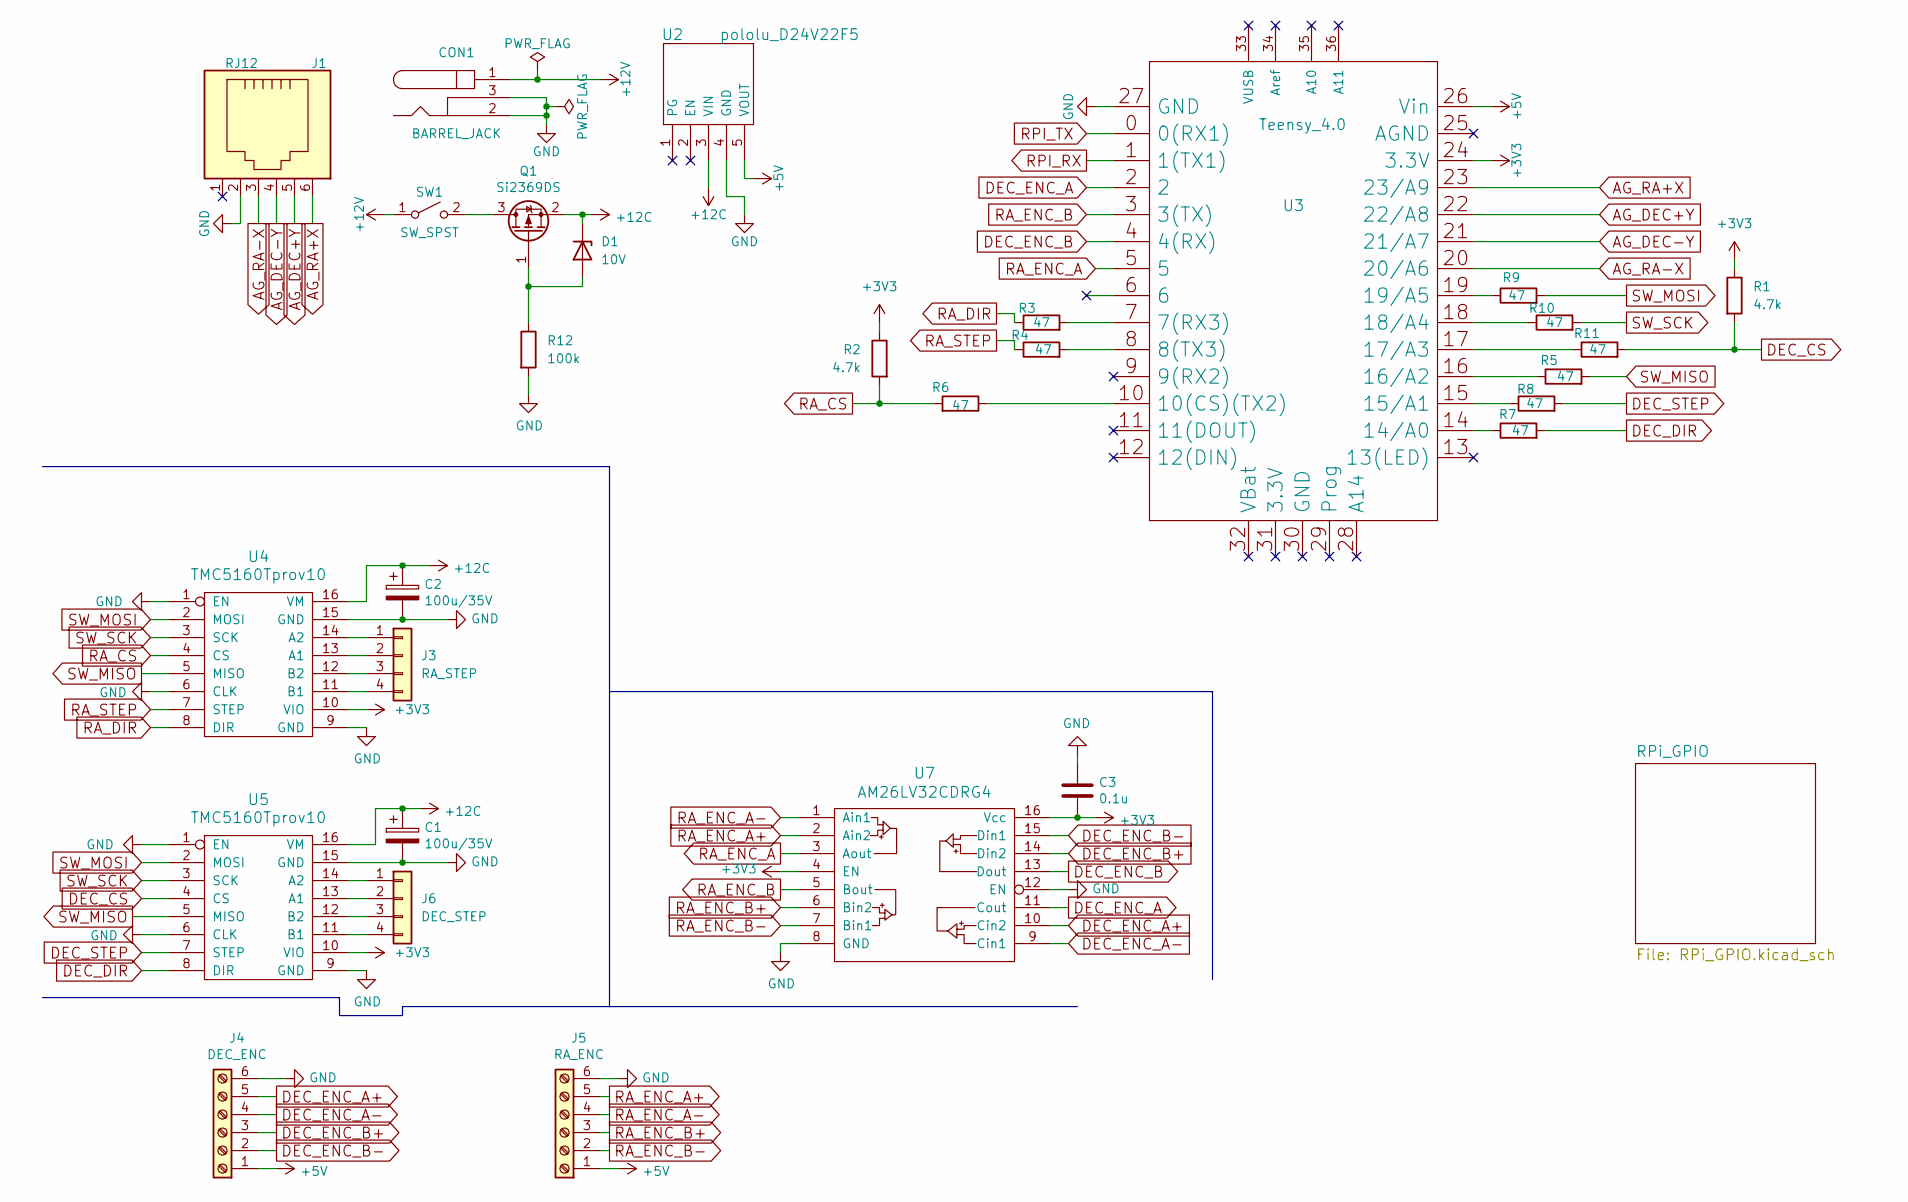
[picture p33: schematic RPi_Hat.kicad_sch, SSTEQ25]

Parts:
C1, C2: 100u/35V; CP_Radial_D6.3mm_P2.50mm
C3: 0.1u; C_0603
CON1: BARREL_JACK; POWER_JACK_PTH
D1: 10V; D_SOD-123
J1: RJ12; RJ11-6
J3: RA_STEP; JST_XH_B4B-XH-A_1x04_P2.50mm_Vertical
J4: DEC_ENC; JST_XH_B6B-XH-A_1x06_P2.50mm_Vertical
J5: RA_ENC; JST_XH_B6B-XH-A_1x06_P2.50mm_Vertical
J6: DEC_STEP; JST_XH_B4B-XH-A_1x04_P2.50mm_Vertical
Q1: Si2369DS; SOT-23
R1, R2: 4.7k; R_0603_1608Metric
R3, R4, R5, R6, R7, R8, R9, R10, R11: 47; R_0603_1608Metric
R12: 100k; R_0603_1608Metric
SW1: SW_SPST; PWR_SWITCH_RA1H1C112R
U2: pololu_D24V22F5
U3: Teensy_4.0; Teensy-3.1
U4, U5: TMC5160Tprov10; pololu_a4988
U7: AM26LV32CDRG4; SOIC-16_3.9x9.9mm_Pitch1.27mm

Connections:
+3V3: C3.2, R1.1, R2.1, U3.24 (3.3V), U4.10 (VIO), U5.10 (VIO), U7.4 (EN), U7.16 (Vcc)
+5V: J4.1, J5.1, U2.5 (VOUT), U3.26 (Vin); also elsewhere on the board
+12C: C1.1, C2.1, D1.1 (K), Q1.2 (S), U2.3 (VIN), U4.16 (VM), U5.16 (VM)
+12V: CON1.1, SW1.1 (A)
AG_DEC+Y: J1.5, U3.22 (22/A8)
AG_DEC-Y: J1.4, U3.21 (21/A7)
AG_RA+X: J1.6, U3.23 (23/A9)
AG_RA-X: J1.3, U3.20 (20/A6)
DEC_CS: R1.2, R11.2, U5.4 (CS)
DEC_DIR: R7.2, U5.8 (DIR)
DEC_ENC_A: U3.2, U7.11 (Cout)
DEC_ENC_A+: J4.5, U7.10 (Cin2)
DEC_ENC_A-: J4.4, U7.9 (Cin1)
DEC_ENC_B: U3.4 (4(RX)), U7.13 (Dout)
DEC_ENC_B+: J4.3, U7.14 (Din2)
DEC_ENC_B-: J4.2, U7.15 (Din1)
DEC_STEP: R8.2, U5.7 (STEP)
GND: C1.2, C2.2, C3.1, CON1.2, CON1.3, J1.2, J4.6, J5.6, R12.2, U2.4 (GND), U3.27 (GND), U4.1 (EN), U4.6 (CLK), U4.9 (GND), U4.15 (GND), U5.1 (EN), U5.6 (CLK), U5.9 (GND), U5.15 (GND), U7.8 (GND), U7.12 (EN); also elsewhere on the board
unnamed: D1.2 (A), Q1.1 (G), R12.1
unnamed: J3.1, U4.14 (A2)
unnamed: J3.2, U4.13 (A1)
unnamed: J3.3, U4.12 (B2)
unnamed: J3.4, U4.11 (B1)
unnamed: J6.1, U5.14 (A2)
unnamed: J6.2, U5.13 (A1)
unnamed: J6.3, U5.12 (B2)
unnamed: J6.4, U5.11 (B1)
unnamed: Q1.3 (D), SW1.2 (B)
unnamed: R3.2, U3.7 (7(RX3))
unnamed: R4.2, U3.8 (8(TX3))
unnamed: R6.1, U3.10 (10(CS)(TX2))
unnamed: R7.1, U3.14 (14/A0)
unnamed: R8.1, U3.15 (15/A1)
unnamed: R5.1, U3.16 (16/A2)
unnamed: R11.1, U3.17 (17/A3)
unnamed: R10.1, U3.18 (18/A4)
unnamed: R9.1, U3.19 (19/A5)
RA_CS: R2.2, R6.2, U4.4 (CS)
RA_DIR: R3.1, U4.8 (DIR)
RA_ENC_A: U3.5, U7.3 (Aout)
RA_ENC_A+: J5.5, U7.2 (Ain2)
RA_ENC_A-: J5.4, U7.1 (Ain1)
RA_ENC_B: U3.3 (3(TX)), U7.5 (Bout)
RA_ENC_B+: J5.3, U7.6 (Bin2)
RA_ENC_B-: J5.2, U7.7 (Bin1)
RA_STEP: R4.1, U4.7 (STEP)
RPI_RX: U3.1 (1(TX1)); also elsewhere on the board
RPI_TX: U3.0 (0(RX1)); also elsewhere on the board
SW_MISO: R5.2, U4.5 (MISO), U5.5 (MISO)
SW_MOSI: R9.2, U4.2 (MOSI), U5.2 (MOSI)
SW_SCK: R10.2, U4.3 (SCK), U5.3 (SCK)

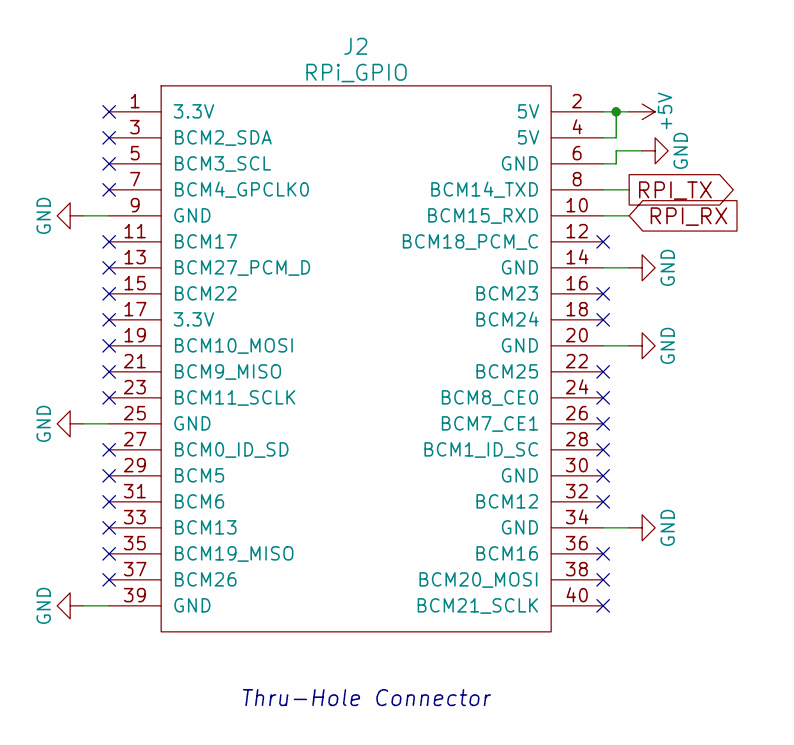
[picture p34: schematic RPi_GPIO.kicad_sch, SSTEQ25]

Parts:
J2: RPi_GPIO; Pin_Header_Straight_2x20

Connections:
+5V: J2.2 (5V), J2.4 (5V); also elsewhere on the board
GND: J2.6 (GND), J2.9 (GND), J2.14 (GND), J2.20 (GND), J2.25 (GND), J2.34 (GND), J2.39 (GND); also elsewhere on the board
RPI_RX: J2.10 (BCM15_RXD); also elsewhere on the board
RPI_TX: J2.8 (BCM14_TXD); also elsewhere on the board

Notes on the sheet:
Thru-Hole Connector

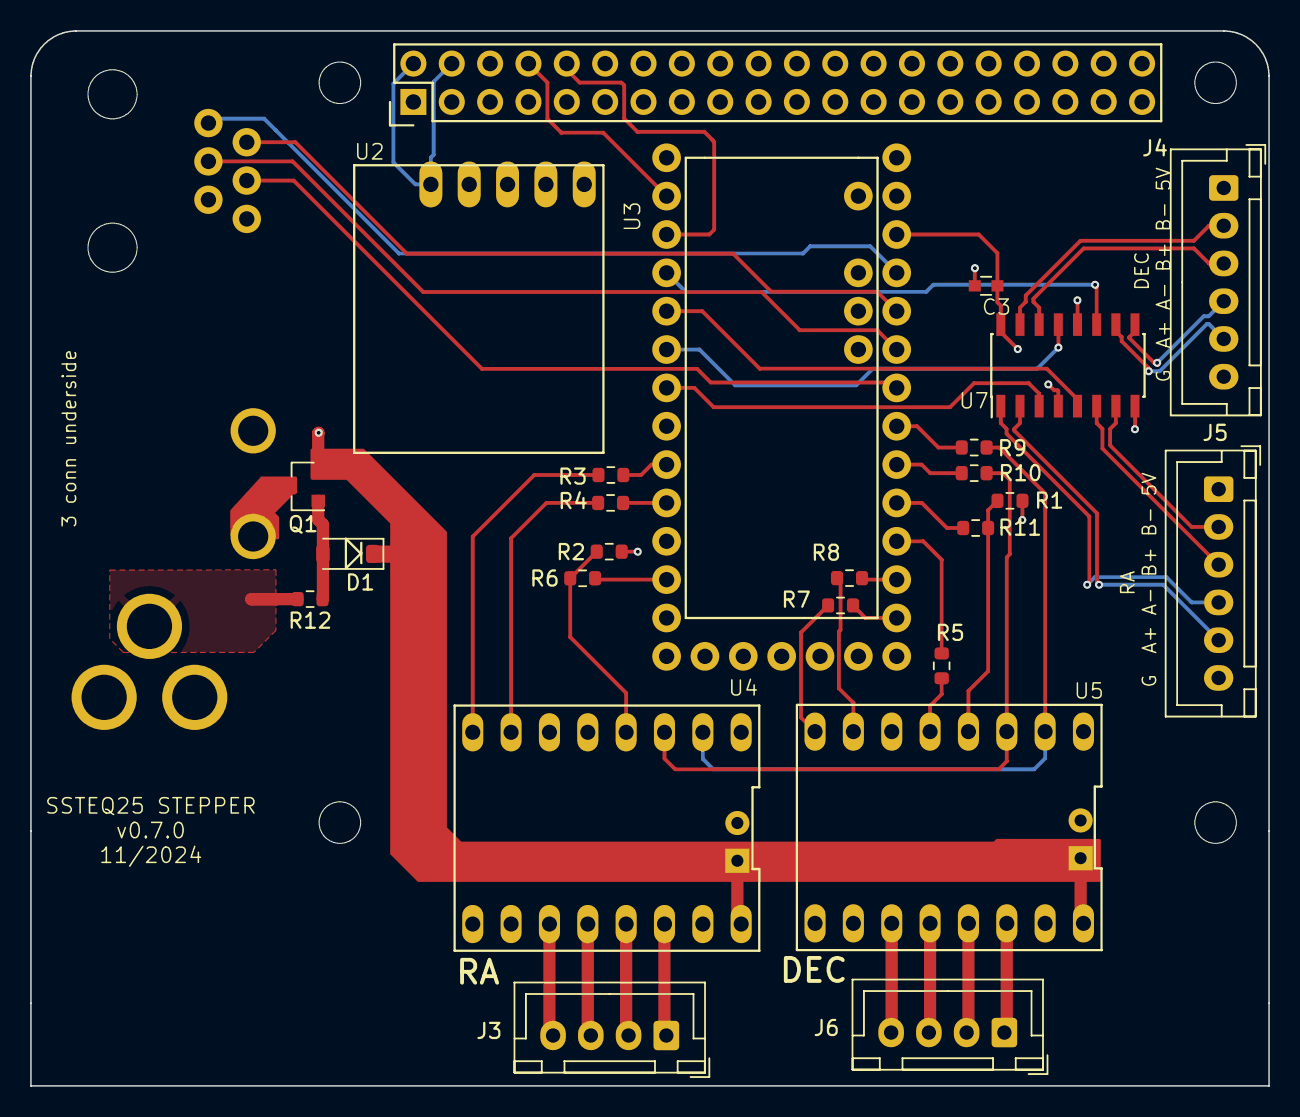
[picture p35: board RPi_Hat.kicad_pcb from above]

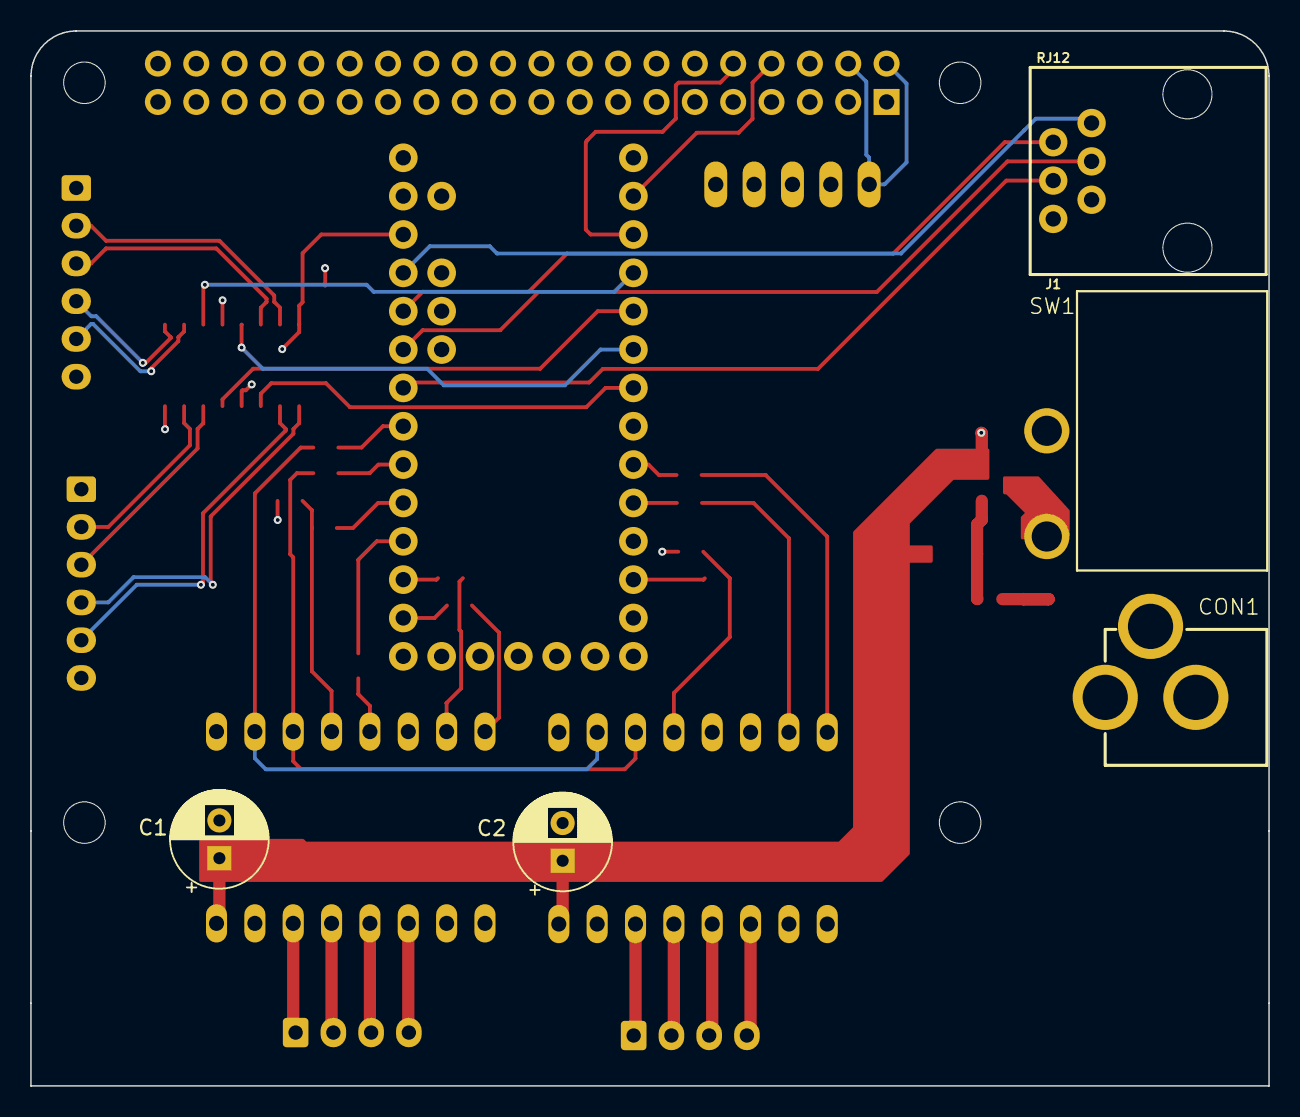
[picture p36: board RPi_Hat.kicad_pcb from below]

Board: 4 copper layers, 82.0 x 69.9 mm, 30 parts (5 on the bottom side), 51 nets.

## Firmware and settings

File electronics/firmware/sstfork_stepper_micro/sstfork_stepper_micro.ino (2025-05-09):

#include <Wire.h>
#include <inttypes.h>
#include <stdint.h>

#include "command.h"
#include "forkmount.h"
#include "stepper.h"

const char *sstversion = "v1.1.0";
Stepper *raStepper = NULL;
Stepper *decStepper = NULL;


static const int RA_ENC_A_PIN = 5;
static const int RA_ENC_B_PIN = 3;
static const int DEC_ENC_A_PIN = 2;
static const int DEC_ENC_B_PIN = 4;

static const int RA_DIR_PIN = 7;
static const int RA_STEP_PIN = 8;
static const int RA_CS_PIN = 10;
static const int RA_MISO_PIN = 16;
static const int RA_SCK_PIN = 18;
static const int RA_MOSI_PIN = 19;

static const int DEC_DIR_PIN = 14;
static const int DEC_STEP_PIN = 15;
static const int DEC_CS_PIN = 17;
static const int DEC_MISO_PIN = 16;
static const int DEC_SCK_PIN = 18;
static const int DEC_MOSI_PIN = 19;

static const int LED_PIN = 13;

const static int AUTOGUIDE_DEC_NEGY_PIN = 21;
const static int AUTOGUIDE_DEC_POSY_PIN = 22;
const static int AUTOGUIDE_RA_NEGX_PIN = 20;
const static int AUTOGUIDE_RA_POSX_PIN = 23;

bool sst_debug = false;

static Command* piCommand = NULL;
static Command* usbCommand = NULL;
IntervalTimer stepperTimer;

void autoguide_init() {
  pinMode(AUTOGUIDE_DEC_NEGY_PIN, INPUT);
  digitalWrite(AUTOGUIDE_DEC_NEGY_PIN, HIGH);
  pinMode(AUTOGUIDE_DEC_POSY_PIN, INPUT);
  digitalWrite(AUTOGUIDE_DEC_POSY_PIN, HIGH);
  pinMode(AUTOGUIDE_RA_NEGX_PIN, INPUT);
  digitalWrite(AUTOGUIDE_RA_NEGX_PIN, HIGH);
  pinMode(AUTOGUIDE_RA_POSX_PIN, INPUT);
  digitalWrite(AUTOGUIDE_RA_POSX_PIN, HIGH);
}

/**
 * When first powered up. sets up serial, sstvars, stepper, console, resets
 * tracker.
 */
void setup() {
  pinMode(DEC_CS_PIN, OUTPUT);
  digitalWrite(DEC_CS_PIN, HIGH);
  pinMode(RA_CS_PIN, OUTPUT);
  digitalWrite(RA_CS_PIN, HIGH);
  pinMode(LED_PIN, OUTPUT);
  digitalWrite(LED_PIN, HIGH);

  while (!Serial && millis() < 2000) {

  }
  digitalWrite(LED_PIN, LOW);
  if (Serial) {
    Serial.begin(115200);
    usbCommand = new Command(&Serial);
  }
  Serial1.begin(115200);
  piCommand = new Command(&Serial1);

  delay(1000);
  if (Serial) {
    DEBUG_SERIAL.println("Begin");
  }
  //SPI.begin();

  decStepper = new Stepper(DEC_DIR_PIN, DEC_STEP_PIN,
                           DEC_CS_PIN, DEC_MISO_PIN, DEC_MOSI_PIN, DEC_SCK_PIN, 
                           2, DEC_ENC_A_PIN, DEC_ENC_B_PIN, 1);
  raStepper = new Stepper(RA_DIR_PIN, RA_STEP_PIN,
                          RA_CS_PIN, RA_MISO_PIN, RA_MOSI_PIN, RA_SCK_PIN, 
                          1, RA_ENC_A_PIN, RA_ENC_B_PIN, 0);

  //raStepper->setSpeed(0.0);
  //decStepper->setSpeed(0.0);
  autoguide_init();
  stepperTimer.begin(update, 4);
  if (Serial && usbCommand != NULL) {
    Serial.print(F("StarSync Tracker Fork Mount "));
    Serial.println(sstversion);
    Serial.print("$ ");
  }
  Serial1.print(F("StarSync Tracker Fork Mount "));
  Serial1.println(sstversion);
  Serial1.print("$ ");
}

uint8_t status = 0;
uint8_t debounce_status = 255;
uint8_t prev_status = 255;
uint8_t rate_state = 0;

const uint8_t AG_POSY_MASK = 0;
const uint8_t AG_NEGY_MASK = 1;
const uint8_t AG_NEGX_MASK = 2;
const uint8_t AG_POSX_MASK = 3;

unsigned long lastDebounceTime = 0;
unsigned long debounceDelay = 50;

void autoguide_read() {
  status = digitalRead(AUTOGUIDE_DEC_POSY_PIN) << AG_POSY_MASK;
  status |= digitalRead(AUTOGUIDE_DEC_NEGY_PIN) << AG_NEGY_MASK;
  status |= digitalRead(AUTOGUIDE_RA_NEGX_PIN) << AG_NEGX_MASK;
  status |= digitalRead(AUTOGUIDE_RA_POSX_PIN) << AG_POSX_MASK;
}

void update() {
  raStepper->update();
  decStepper->update();
}

void autoguide_run() {
  if (!raStepper->guidingEnabled() || !decStepper->guidingEnabled()) {
    return;
  }

  autoguide_read();
  // If change
  if (status != debounce_status) {
    debounce_status = status;
    lastDebounceTime = millis();
  }

  if (status != prev_status && (millis() - lastDebounceTime) > debounceDelay) {
    if (sst_debug) {
      Serial1.print("status != prev_status and debounced: ");
      Serial1.println(status);
    }

    // Low means pressed except for rate switch

    prev_status = status;

    // If no directions are pressed we are just tracking
    if ((status & 0x0F) == 0x0F) {
      raStepper->guide(0);
      decStepper->guide(0);
      if (sst_debug) {
        Serial1.print("no buttons: ");
      }
    } else {
      if (!(status & (1 << AG_POSY_MASK))) {
        decStepper->guide(1);
        if (sst_debug) {
          Serial1.print("DEC up ");
        }
      } else if (!(status & (1 << AG_NEGY_MASK))) {
        decStepper->guide(-1);
        if (sst_debug) {
          Serial1.print("DEC down ");
        }
      } else {
        decStepper->guide(0);
      }

      if (!(status & (1 << AG_POSX_MASK))) {
        raStepper->guide(1);
        if (sst_debug) {
          Serial1.print("RA Right ");
        }

      } else if (!(status & (1 << AG_NEGX_MASK))) {
        raStepper->guide(-1);
        if (sst_debug) {
          Serial1.print("RA Left");
        }
      } else {
        raStepper->guide(0);
      }
    }
  }
}


/**
 * Program loop.
 */
void loop() {
  // Serial.println("Loop");
  autoguide_run();
  piCommand->read();
  if (Serial) {
    if (usbCommand == NULL) {
      Serial.begin(115200);
      usbCommand = new Command(&Serial);
    }
    usbCommand->read();
  }
}

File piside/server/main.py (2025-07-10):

import update_python_paths
import time
import re
import copy
import datetime
import json
import logging
import os
import socket
import subprocess
import sys
import tempfile
import threading
import traceback
import zipfile
import argparse
import vmc_simulator
from functools import wraps, update_wrapper

import astropy.units as u
from astropy.coordinates import ICRS, TETE, AltAz
from skyconv_hadec import HADec
from astropy.utils import iers
from flask import Flask, redirect, jsonify, request, make_response, url_for, send_from_directory
from flask_compress import Compress
from werkzeug.serving import make_ssl_devcert

import control
import db
import handpad_menu
import handpad_server
import lx200proto_server
import network
import settings
import skyconv

iers.conf.auto_download = False
iers.auto_max_age = None

avahi_process = None

power_thread_quit = False

st_queue = None
app = Flask(__name__, static_folder='../client_refactor/dist/')
logging.getLogger('werkzeug').setLevel(logging.ERROR)
# socketio = SocketIO(app, async_mode='threading', logger=False, engineio_logger=False)
settings_json_lock = threading.RLock()

pointing_logger = settings.get_logger('pointing')

RELAY_PIN = 6
SWITCH_PIN = 5

compress = Compress()
update_python_paths.keep_import()


# Sets up power switch
# TODO: disable power switch for simulation
def run_power_switch():
    pass
    # try:
    #     import RPi.GPIO as GPIO
    #     GPIO.setmode(GPIO.BCM)
    #     GPIO.setup(RELAY_PIN, GPIO.OUT)
    #     GPIO.setup(SWITCH_PIN, GPIO.IN, pull_up_down=GPIO.PUD_UP)
    #     GPIO.output(RELAY_PIN, True)
    #
    #     while not power_thread_quit:
    #         time.sleep(0.1)
    #         if GPIO.input(SWITCH_PIN) == 0:
    #             continue
    #         time.sleep(0.1)
    #         if GPIO.input(SWITCH_PIN) == 1:
    #             subprocess.run(['sudo', 'shutdown', '-h', 'now'])
    #
    # except ImportError:
    #     # We are probably in simulation
    #     print("Warning: Can't use power switch.")


@app.context_processor
def override_url_for():
    """
    Generate a new token on every request to prevent the browser from
    caching static files.
    """
    return dict(url_for=dated_url_for)


def dated_url_for(endpoint, **values):
    if endpoint == 'static':
        filename = values.get('filename', None)
        if filename:
            file_path = os.path.join(app.root_path,
                                     endpoint, filename)
            values['q'] = int(os.stat(file_path).st_mtime)
    return url_for(endpoint, **values)


def nocache(view):
    @wraps(view)
    def no_cache(*args, **kwargs):
        response = make_response(view(*args, **kwargs))
        response.headers['Last-Modified'] = datetime.datetime.now()
        response.headers['Cache-Control'] = 'no-store, no-cache, must-revalidate, post-check=0, pre-check=0, max-age=0'
        response.headers['Pragma'] = 'no-cache'
        response.headers['Expires'] = '-1'
        return response

    return update_wrapper(no_cache, view)


@app.route('/api/version')
@nocache
def version():
    return jsonify({"version": control.version, "version_date": control.version_date_str})


@app.route('/api/settings')
@nocache
def settings_get():
    s = copy.deepcopy(settings.settings)
    s['encoder_logging'] = control.encoder_logging_enabled
    s['calibration_logging'] = settings.runtime_settings['calibration_logging']
    if not s['location']:
        s['location'] = {
            'lat': control.DEFAULT_LAT_DEG,
            'long': control.DEFAULT_LON_DEG,
            'name': 'Unset Location'
        }
    # print(s)
    return jsonify(s)


@app.route('/api/settings_dl')
@nocache
def settings_dl_get():
    return send_from_directory(directory='./', filename='settings.json', as_attachment=True,
                               attachment_filename='ssteq25_settings.json')


@app.route('/api/settings_dl', methods=['POST'])
@nocache
def settings_dl_post():
    file = request.files['file']
    with tempfile.TemporaryFile(suffix='.json') as tfile:
        file.save(tfile)
        tfile.seek(0)
        json.load(tfile)  # just to check it is at least a json
        tfile.seek(0)
        settings.copy_settings(tfile)
    if not settings.is_simulation():
        t = threading.Timer(5, reboot)
        t.start()
    return 'Updated Settings'


@app.route('/api/hostname')
@nocache
def hostname_get():
    return jsonify({'hostname': socket.gethostname()})


@app.route('/api/shutdown', methods=['PUT'])
@nocache
def shutdown_put():
    control.set_shutdown()
    return 'Shutdown', 200


@app.route('/api/logger', methods=['GET'])
@nocache
def logger_get():
    logger_name = request.args.get('name')
    if logger_name == 'pointing':
        pointing_logger.handlers[0].flush()
        return send_from_directory(os.path.join(os.path.expanduser('~'), 'logs'), 'pointing.log', as_attachment=True,
                                   attachment_filename='pointing_log.txt')
    elif logger_name == 'calibration':
        ret = []
        for row in control.calibration_log:
            # TODO: just support ra/dec right now add others
            if 'sync' in row and 'slewto' in row and 'slewfrom' in row:
                ret.append({
                    'slewfrom': {'ra': row['slewfrom'].ra.deg, 'dec': row['slewfrom'].dec.deg},
                    'slewto': {'ra': row['slewto'].ra.deg, 'dec': row['slewto'].dec.deg},
                    'sync': {'ra': row['sync'].ra.deg, 'dec': row['sync'].dec.deg}
                })
        return jsonify(ret)
    elif logger_name == 'encoder':
        if control.encoder_logging_enabled:
            control.encoder_logging_file.flush()
        return send_from_directory(os.path.join(os.path.expanduser('~'), 'logs'), 'stepper_encoder.csv',
                                   as_attachment=True,
                                   attachment_filename='stepper_encoder.csv')


@app.route('/api/logger', methods=['DELETE'])
@nocache
def logger_clear():
    args = request.json
    logger_name = args.get('name')
    if logger_name == 'encoder':
        control.encoder_logging_clear = True
        return 'Clearing encoder log', 200
    elif logger_name == 'calibration':
        control.calibration_log = []
        return 'Calibration log cleared', 200
    return 'Invalid logger', 400


@app.route('/api/logger', methods=['PUT'])
@nocache
def logger_put():
    args = request.json
    logger_name = args.get('name')
    enabled = args.get('enabled')
    if logger_name == 'encoder':
        control.start_stop_encoder_logger(enabled)
        if enabled:
            return 'Starting logger', 200
        else:
            return 'Stopping logging', 200
    elif logger_name == 'calibration':
        settings.runtime_settings['calibration_logging'] = enabled
        return 'Calibration setting set', 200
    else:
        return 'Invalid logger', 400
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

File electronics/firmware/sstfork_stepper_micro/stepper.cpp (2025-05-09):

#include "stepper.h"
#include "forkmount.h"

static const int MICROSTEPS_IN_SINGLESTEP = 32;
static const float CURRENT_TO_RMS = 0.7071;  // 1/sqrt(2) see page 74 of datasheet
// GLOBALSCALER/256  *  (CS + 1)/32  *  V_FS/R_SENSE  *  1/sqrt(2)
static const bool STEP_DEDGE = true; // Step on rising or falling edge

template<typename T> int sgn(T val) {
  return (T(0) < val) - (val < T(0));
}

Stepper::Stepper(const int _dir_pin, const int _step_pin, 
                 const int _cs_pin, const int _miso_pin, const int _mosi_pin, const int _sck_pin,
                 uint8_t enc_chan, uint16_t enc_apin, uint16_t enc_bpin, uint8_t timer) {
  id = timer;
  dir_pin = _dir_pin;
  step_pin = _step_pin;
  if (enc_apin != enc_bpin) {
    enc = new QuadEncoder(enc_chan, enc_apin, enc_bpin);
    enc->setInitConfig();
    enc->init();
  }
  pinMode(dir_pin, OUTPUT);
  pinMode(step_pin, OUTPUT);
  //driver = new TMC5160Stepper(_cs_pin);
  //driver = new TMC5160Stepper(_cs_pin, 0.075f);
  //driver = new TMC5160Stepper(_cs_pin);

  driver = new TMC5160Stepper(_cs_pin, R_SENSE, _mosi_pin, _miso_pin, _sck_pin);
  //driver = new TMC5160Stepper(_cs_pin, _mosi_pin, _miso_pin, _sck_pin);

  driver->setSPISpeed(1000);
  driver->begin();
  delay(100);
  this->test_connection();
  driver->toff(5);
  this->setCurrents(true);

  driver->en_pwm_mode(true);
  driver->pwm_autoscale(true);
  driver->intpol(true);
  
  driver->microsteps(MICROSTEPS_IN_SINGLESTEP);
  driver->dedge(STEP_DEDGE);
  single_step = false;

  setStepDirection(false);
  backlashCounter=9999999;
  for(int i = 0; i < 8; i++) {
    this->step(true);
    delay(50);
  }
  setStepDirection(true);
  backlashCounter=9999999;
  for(int i = 0; i < 8; i++) {
    this->step(true);
    delay(50);
  }

  while(driver->microsteps() != MICROSTEPS_IN_SINGLESTEP) {
    driver->microsteps(MICROSTEPS_IN_SINGLESTEP);
  }

}

uint8_t Stepper::test_connection() {
  uint8_t tcv = driver->test_connection();
  while(tcv != 0) {
    DEBUG_SERIAL.print("WARN: Test connection failed ");
    DEBUG_SERIAL.print(id);
    DEBUG_SERIAL.print(", ");
    DEBUG_SERIAL.println(tcv);
    delay(1000);
    tcv = driver->test_connection();
  } 
  DEBUG_SERIAL.print("Test Connection Good ");
  DEBUG_SERIAL.println(id);
  return tcv;
}

void Stepper::setSpeed(float speed) {
  DEBUG_SERIAL.println(driver->DRV_STATUS(), BIN);
  cli();
  sp_speed = speed;
  timer = 0;
  v0 = vt;
  sei();
}

float Stepper::getSpeed() {
  float ret;
  cli();
  ret = vt;
  sei();
  return ret;
}

long Stepper::getPosition() {
  long ret;
  cli();
  ret = x0;
  sei();
  return ret;
}

void Stepper::getEncoder(stepper_encoder_t& encodervalues) {
  cli();
  encodervalues.value = last_encoder;
  encodervalues.steps_in_pulse = steps_in_pulse;
  encodervalues.prev_steps_in_pulse = steps_in_pulse;
  sei();
}

void Stepper::setInvertedStepping(bool inverted) {
  cli();
  inv_direction = inverted;
  setStepDirection(mode_forward);
  sei();
}

bool Stepper::getInvertedStepping() {
  return inv_direction;
}

void Stepper::setSingleStepThreshold(long steps_per_sec) {
  cli();
  micro_threshold_v = steps_per_sec;
  sei();
}

long Stepper::getSingleStepThreshold() {
  cli();
  long ret = micro_threshold_v;
  sei();
  return ret;
}

void Stepper::enableEncoder(bool enabled) {
  enc_enabled = true;
}

bool Stepper::encoderEnabled() {
  return enc_enabled;
}


void Stepper::setStepDirection(bool forward) {
  cli();
  if (forward) {
    if (!inv_direction) {
      digitalWrite(dir_pin, HIGH);
    } else {
      digitalWrite(dir_pin, LOW);
    }
    if(!mode_forward && backlash > 0 && backlashSpeed > 0) {
      backlashCounter = 0;
    }
    mode_forward = true;
  } else {
    if (!inv_direction) {
      digitalWrite(dir_pin, LOW);
    } else {
      digitalWrite(dir_pin, HIGH);
    }
    if(mode_forward && backlash > 0 && backlashSpeed > 0) {
      backlashCounter = 0;
    }
    mode_forward = false;
  }
  sei();
}

void Stepper::setStepResolution(bool _single_step) {
  cli();
  if (_single_step && !single_step) {
    single_step = true;
    while(driver->microsteps() != 0) {
      driver->microsteps(0);
    }

    // At full step every step is X microsteps
    stepResolution = MICROSTEPS_IN_SINGLESTEP;
  } else if (!_single_step && single_step) {
    single_step = false;
    while(driver->microsteps() != MICROSTEPS_IN_SINGLESTEP) {
      driver->microsteps(MICROSTEPS_IN_SINGLESTEP);
    }
    // Every micro step is 1 microsteps
    stepResolution = 1;
  }
  sei();
}

void Stepper::step(bool counters) {
  cli();
  bool on = !digitalRead(step_pin);
  digitalWrite(step_pin, on);
  if (counters && (STEP_DEDGE || on)) {
    if (mode_forward) {
      x0 += stepResolution;
    } else {
      x0 -= stepResolution;
    }
  }
  if (enc_enabled) {
    long encV = enc->read();
    if (encV != last_encoder) {
      prev_steps_in_pulse = steps_in_pulse;
      steps_in_pulse = 0;
      if(counters) {
        last_encoder = encV;
      } else {
        enc->write(last_encoder);
      }
    } else {
      if (STEP_DEDGE || on) {
        if (mode_forward) {
          steps_in_pulse += stepResolution;
        } else {
          steps_in_pulse -= stepResolution;
        }
      }
    }
  }
  sei();
}

void Stepper::setMaxAccel(float _accell_tpss) {
  cli();
  accell_tpss = _accell_tpss;
  sei();
}

float Stepper::getMaxAccel() {
  cli();
  float ret = accell_tpss;
  sei();
  return ret;
}

void Stepper::setMaxSpeed(float _max_tps) {
  cli();
  max_v = _max_tps;
  sei();
}

float Stepper::getMaxSpeed() {
  float ret;
  cli();
  ret = max_v;
  sei();
  return ret;
}

bool Stepper::enabled() {
  return stepper_enabled;
}

void Stepper::enable(bool _enable) {
  stepper_enabled = _enable;
}

void Stepper::setGuideRate(long _guideRate) {
  cli();
  guide_rate = _guideRate;
  sei();
}

long Stepper::getGuideRate() {
  long ret;
  cli();
  ret = guide_rate;
  sei();
  return ret;
}

void Stepper::guide(int direction) {
  cli();
  guiding = direction;
  sei();
}

void Stepper::guidingEnable(bool enable) {
  guiding_enabled = enable;
}

bool Stepper::guidingEnabled() {
  return guiding_enabled;
}

void Stepper::setRunCurrent(float _run_current) {
  cli();
  run_current = _run_current > 1 ? _run_current : 1;
  setCurrents(true);
  sei();
}

void Stepper::setMedCurrent(float _med_current) {
  cli();
  med_current = _med_current > 1 ? _med_current : 1;
  setCurrents(true);
  sei();
}

void Stepper::setMedCurrentThreshold(float _med_current_threshold) {
  cli();
  med_current_threshold = _med_current_threshold;
  setCurrents(true);
  sei();
}

void Stepper::setHoldCurrent(float _hold_current) {
  cli();
  // Setting 0 current doesn't work (at least if not doing ihold)
  hold_current = _hold_current > 1 ? _hold_current : 100;
  // DEBUG_SERIAL.print("Set hold current: ");
  // DEBUG_SERIAL.println(hold_current);
  setCurrents(true);
  sei();
}
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

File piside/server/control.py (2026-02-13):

"""
control methods for the mount.
"""

import threading
from functools import partial
import time
import traceback
import os

import psutil
import random

# from sstutil import ProfileTimer as PT

import datetime
from astropy.coordinates import EarthLocation, AltAz, TETE, ICRS
from skyconv_hadec import HADec
from astropy.time import Time as AstroTime
import astropy.units as u
import math
import socket
import json
import stepper_control
import pointing_model
import pendulum
import subprocess

from timezonefinder import TimezoneFinder

import skyconv
import settings
import motion
import typing
import simple_pid

version = "0.0.37"
version_short = "0.0"
version_date_str = "Apr 26 2021"

SIDEREAL_RATE = 0.004178074568511751  # 15.041"/s
AXIS_RA = 1
AXIS_DEC = 2

timers = {}
OPPOSITE_MANUAL = {"left": "right", "right": "left", "up": "down", "down": "up"}
DEFAULT_PARK = {"az": 180, "alt": 0}
slew_lock = threading.RLock()
set_last_slew_lock = threading.RLock()
manual_lock = threading.RLock()
time_location_lock = threading.RLock()
status_interval = None
inited = False
slewing = False
stepper: typing.Optional[stepper_control.StepperControl] = None

park_sync = False

cancel_slew = False
last_status: typing.Optional[dict] = None
last_target = {
    "ra": None,
    "dec": None,
    "ha": None,
    "alt": None,
    "az": None,
    "frame": None,
    "parking": False,
}

ra_encoder_error = None
dec_encoder_error = None

encoder_logging_enabled = False
encoder_logging_file: typing.Optional[typing.TextIO] = None
encoder_logging_clear = False
encoder_logging_interval = None

# Last sync or slew info, if tracking sets radec, else altaz.
last_slew: typing.Dict[str, typing.Union[None, TETE, ICRS, AltAz]] = {
    "tete": None,
    "icrs": None,
    "altaz": None,
}

pointing_logger = settings.get_logger("pointing")

calibration_log = []


def synchronized(lock):
    """Synchronization decorator."""

    def wrap(f):
        def newFunction(*args, **kw):
            lock.acquire()
            try:
                return f(*args, **kw)
            finally:
                lock.release()

        return newFunction

    return wrap


def set_last_slew(coord):
    with set_last_slew_lock:
        if not coord:
            last_slew["tete"] = None
            last_slew["altaz"] = None
        else:
            if settings.runtime_settings["tracking"]:
                tete = skyconv.to_tete(
                    coord, overwrite_time=True, obstime=AstroTime.now()
                )
                icrs = skyconv.to_icrs(tete)
                last_slew["tete"] = tete
                last_slew["icrs"] = icrs
                last_slew["altaz"] = None
            else:
                altaz = skyconv.to_altaz(coord)
                last_slew["tete"] = None
                last_slew["icrs"] = None
                last_slew["altaz"] = altaz


sls_debounce = None


def _set_last_slew_none_run():
    global sls_debounce
    # print('Running set_last_slew(None)')
    set_last_slew(None)
    sls_debounce = None


def set_last_slew_none():
    global sls_debounce
    if sls_debounce is None:
        sls_debounce = threading.Timer(0.5, _set_last_slew_none_run)
        sls_debounce.start()


def _ra_aminpsec_to_stppsec(arcmin_per_second):
    """
    arcmin/second to steps/second for RA
    :param arcmin_per_second:
    :return:
    """
    steps_per_degree = settings.settings["ra_ticks_per_degree"]
    return steps_per_degree * arcmin_per_second / 60.0


def _ra_asecpsec_to_stppsec(arcsec_per_second):
    """
    arcsec/second to steps/second for RA
    :param arcmin_per_second:
    :return:
    """
    steps_per_degree = settings.settings["ra_ticks_per_degree"]
    return steps_per_degree * arcsec_per_second / (60.0 * 60.0)


def _dec_aminpsec_to_stppsec(arcmin_per_second):
    """
    arcmin/second to steps/second for Dec
    :param arcmin_per_second:
    :return:
    """
    steps_per_degree = settings.settings["dec_ticks_per_degree"]
    return steps_per_degree * arcmin_per_second / 60.0


def _dec_asecpsec_to_stppsec(arcsec_per_second):
    """
    arcmin/second to steps/second for Dec
    :param arcmin_per_second:
    :return:
    """
    steps_per_degree = settings.settings["dec_ticks_per_degree"]
    return steps_per_degree * arcsec_per_second / (60.0 * 60.0)


def sync(coord):
    """
    :param coord:
    :return:
    """
    global park_sync
    status = calc_status(stepper.get_status())
    obstime = AstroTime.now()
    with set_last_slew_lock:
        set_last_slew(coord)
        hadec = skyconv.to_hadec(coord, obstime=obstime)
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

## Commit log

2018-01-16 Fixed coordinates around poles.
    [control.py, main.py]
2018-03-12 Fixed disable autoguide error.
    [control.py]
2018-03-16 Fixed when button is pressed and you move mouse off of button.
2018-03-18 redlights color styleing, manual slew acceleration, better goto acceleration, fix on simulation for raspeed, guiding rate is change of rate instead of set rate.
    [control.py, main.py]
2018-03-18 Disable auto download and fix setting max speed.
    [control.py, main.py]
2018-03-23 Fixed reading from micro issues that could cause manual slew to get stuck.
    [control.py]
2018-03-23 Added some missing print_prompts in simulator.
    [main.py]
2018-03-24 Displays percent error on sync. Fix missing prompt in micro firmware.
    [command.cpp, control.py, main.py]
2018-03-24 Slewto and set action in search are buttons. Set location in search location is button.
2018-04-03 Move around sync/slew in object search. Change color of buttons added more icons in buttons. Fixed stellarium server when not synced.
    [control.py, main.py]
2018-04-10 lots of fixes with manual coordinates.
    [main.py]
2018-04-16 Fixed some going back and forth forever, but will implement pid controller next for slewing.
    [control.py]
2018-04-20 Fixes for close slewing.
    [control.py]
2018-06-19 Added kicad electronics
    [RPi_GPIO.sch, RPi_Hat.kicad_pcb, RPi_Hat.sch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]
2018-06-19 RA DEC to M info
    [RPi_Hat.sch]
2018-07-28 Direction buttons change brightness when pressed
2018-08-21 prototype4 electronics
    [RPi_GPIO.sch, RPi_Hat.kicad_pcb, RPi_Hat.sch]
2018-09-03 Note on stepper motor test point voltage added.
    [RPi_Hat.sch]
2018-09-04 Updated notes
    [RPi_Hat.sch]
2018-09-04 Enable power switch detection to shutdown.
    [RPi_Hat.sch]
2018-10-01 Polar align assist calibration image generation.
2018-10-19 Changed monkey patch order to fix a greenlet threading issue
    [main.py]
2018-10-22 Fixed wifi settings when wanting no password.
    [main.py]
2018-11-20 start of a arc_center_find for polar alignment assist calibration.
2018-11-21 updated enclosure
    [ssteq_enclosurev0.3.0.fcstd]
2018-11-21 v0.2.0 enclosure
    [ssteq_enclosurev0.2.0.fcstd]
2018-12-21 Added horizon limit enable disable option. Fixed reloading with hash.
    [control.py, main.py, settings.py]
2019-01-05 Fixed polar align assist with thread mode, added star clicking and setting rotation axises from three point circle.
    [main.py]
2019-01-29 Polar align camera always takes images.
2019-02-22 Add option for different pointing models. A initial pointing model graph showing sync points. paa camera clears directory at start.
2019-02-24 r < 0 case
2019-03-12 Fix starting dnsmasq in autohotspot and ctrl_dnsmasq.
    [main.py, pointing_model.py]
2019-03-15 Kicad files for newest daughter board.
    [RPi_GPIO.sch, RPi_Hat.kicad_pcb, RPi_Hat.sch]
2019-03-19 Made polar alignment more responsive to changes and error reslienant.
    [main.py]
2019-04-12 Added two new pointing models. Added freecad files for electronics enclosure. avahi broadcasting added.
    [ssteq_enclosurev0.6.0_lid.fcstd, ssteq_enclosurev0.6.2.fcstd]
2019-04-12 Encoder counts added to status.
2019-04-14 Added stepper ticks in encoder pulse to status commands.
2019-04-22 encoder changes
    [ssteq_enclosurev0.6.1_lid.fcstd, ssteq_enclosurev0.6.3.fcstd]
2019-04-25 Fix issue where sometimes slew would never finish.
    [control.py, main.py]
2019-06-24 some lx200 protocol fixes
    [control.py, lx200proto_server.py]
2019-07-07 lx200 slewing busy is fixed. Always thinks at park position now, or if no park position set, at 10/180 alt/az.
    [control.py, lx200proto_server.py, main.py]
2019-09-16 Back button sorta works using location.hash
2019-10-07 comment out some debugging prints
2019-10-08 RA and DEC slew in seperate threads. Fixed Coordinate error clearing in UI.
    [control.py, motion.py]
2019-10-10 can plot encoder logs
2019-10-11 More configurable encoder graphs
2019-10-14 missing log update_settings in stepper_control. Logging of last ticks per encoder.
    [control.py, stepper_control.py]
2019-10-14 status gives you last ticks per encoder.
2019-10-14 Fixed default park position
    [control.py]
2019-10-15 Encoder fixes
2019-10-17 added single step switching at high v for faster slewing.
2019-10-22 models don't tottally error when in use.
    [control.py, main.py, skyconv.py]
2019-12-30 Sync changes that can hopfully fix when we can't sync.
    [control.py, lx200proto_server.py, pointing_model.py]
2020-03-02 RA/DEC Motor Disable options
2020-03-03 Motors stop if encoders are not reading.
2020-03-05 Fix dec0deg sign issue in lx200 protocol.
    [lx200proto_server.py]
2020-03-05 Fix hms to deg ra conversion in goto coordinates interface.
    [control.py]
2020-03-11 Added calibration logging feature.
2020-03-20 start of handpad server
    [sst_handpad.kicad_pcb, sst_handpad.sch]
2020-04-08 Handpad changes: display_sleep timeout, communication failure with mount timeout
    [main.py]
2020-06-05 First version of a arduino version of handpad firmware.
2020-06-05 Working version of arduino firmware.
2020-06-06 Updated handpad with bosses and virtical micro, and rotated lcd pins
    [sst_handpad.kicad_pcb, sst_handpad.sch]
2020-06-07 Removed mosfet switching. Seperate DEC/RA encoder headers.
    [RPi_GPIO.sch, RPi_Hat.kicad_pcb, RPi_Hat.sch]
2020-06-22 Handpad alt/az goto menu added. Clear calibration points button added to web.
2020-06-22 Added Sun as a solar system object. commented handpad debug print statements.
2020-07-20 Another try for the fix that makes motor go wrong direction on manual slew first time.
    [command.cpp]
2020-08-04 Fixes: 1) Settings upload read-only issue 2) Wifi settings saving 3) Auto Use GPS if handpad plugged in 4) Adds option to pick from themes, currently default and dark 5) Wifi Client connect dialog go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
    [control.py, handpad_menu.py, handpad_server.py]
2020-08-06 Adds sidereal time to web interfaces. Adds mount info menu in handpad.
2020-08-07 CPU Info (temperature, cpu load, ram usage) added.
2020-08-31 Fix being able to go dec and ra same time with handpad
    [control.py, handpad_server.py]
2020-10-03 Fix prefixed zeros in coordinates input. In object search Catalog search don't need spaces anymore.
    [control.py, main.py]
2020-10-04 cleanup, and should be a real fix for sometime motor direction wrong on startup.
2020-12-12 Fixes with new coordinate system.
    [control.py, handpad_menu.py, lx200proto_server.py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]
2020-12-13 Better unit tests, fixed errors found while unit testing.
    [skyconv.py]
2020-12-14 More fixes found by unit testing.
    [skyconv.py]
2020-12-14 Added unit test for frame args.
2020-12-14 Fixed up model with coordinate changes.
    [control.py, pointing_model.py, skyconv.py]
2020-12-15 Added models and missing files
    [arrow_button.FCStd, bottom.FCStd, bottom_north.FCStd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]
2020-12-29 Fixed negative inputs. Fixed HADec no tracking status. Fixed infinite slew. Added reverse voltage mosfet.
    [RPi_GPIO.sch, RPi_Hat.kicad_pcb, RPi_Hat.sch]
2020-12-29 Added frame to slewing dialog. Fixed network to change /etc/hosts Uses PID controller for settling.
    [control.py, network.py]
2021-01-11 Removed note about jummper cut, was for older drivers.
    [RPi_Hat.sch]
2021-04-26 Fix coordinate conversion for affine model.
    [control.py, skyconv.py]
2021-05-25 Stepper and Brushed Servo boards, stepper uses toshiba driver.
    [RPi_GPIO.sch, RPi_Hat.kicad_pcb, RPi_Hat.sch]
2021-05-25 Updated micro firmware for toshiba driver.
2024-03-02 stepper class using interrupt timers for step/dir instead of loop
2024-06-05 Adding new current options to UI.
2024-06-08 Stepper SPI controller board designed for TMC5160
    [RPi_GPIO.kicad_sch, RPi_GPIO.sch, RPi_Hat.kicad_pcb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]
2024-06-16 Updated JS libs, python, and sim, also support MTC stepper options
2024-06-19 some fixes to lx200 protocol. react18 updates.
    [lx200proto_server.py]
2024-10-09 minimum current of 1ma. Also can force setCurrents().
2024-10-28 Some basic backlash support.
    [command.cpp, main.py, serial_to_ethernet.ino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]
2024-12-23 backlash fixes on serverside
    [control.py, stepper_control.py]
2024-12-24 counts more correct when dedge is on.
    [sstfork_stepper_micro.ino, stepper.cpp]
2024-12-24 Fixed long commands to micro.
    [RPi_Hat.kicad_pcb, RPi_Hat.kicad_sch]
2024-12-25 lx200 protocol socket server is working a little better now.
2025-01-13 Updated microcontroller firmware to use loop time check stepping instead of interrupts.
2025-01-19 Interrupt based stepper->update()
2025-01-20 Backlash with to run in interrupt update method.
    [command.cpp, sstfork_stepper_micro.ino, stepper.cpp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]
2025-02-17 Fixes rare hangup when slewing.
    [control.py, lx200proto_server.py, stepper_control.py]
2025-03-11 Fixed guiding pin assignments.
    [sstfork_stepper_micro.ino, stepper.h]
2025-04-25 move position autoguide is enabled in case there is an exception.
2025-04-28 Fix planet coordinate search.
    [db.py]
2025-07-09 Fixed __str__ in buiemodel.
    [pointing_model.py]
2025-08-03 Added some enclosure render,pcb,schematic images
    [Handpad.ods, PiHatBOM.ods]
2025-08-04 Better model replacement logic.
    [control.py, pointing_model.py, stepper_control.py]
2025-08-04 update print line.
2026-02-13 Some checks to prevent model exceptions
    [control.py, pointing_model.py]
2026-02-15 Remove buffer that caused issue with lx200 protocol.
    [lx200proto_server.py, serial_to_ethernet.ino]
